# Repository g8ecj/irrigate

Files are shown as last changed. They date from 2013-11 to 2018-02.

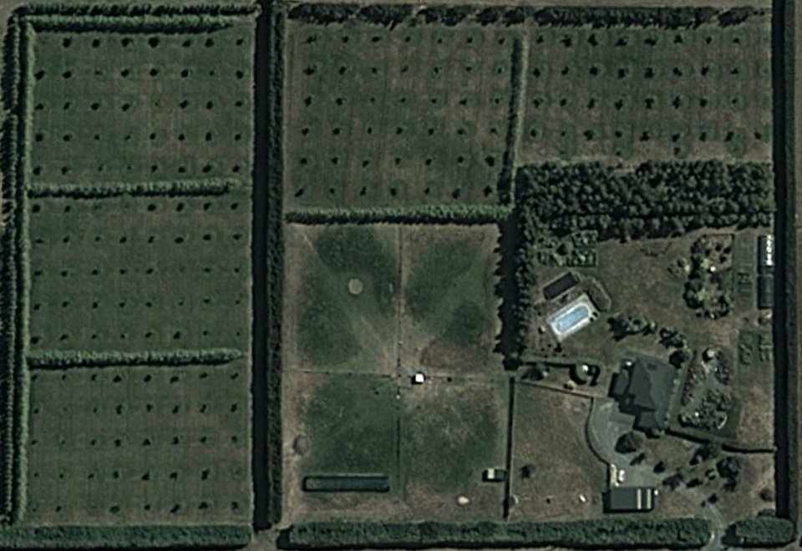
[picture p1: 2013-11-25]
www/zones.jpg

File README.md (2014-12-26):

This is the irrigation controller. It has evolved over a period of some 5 years, the
requirements have changed (and been expanded) and the hardware changed such that a router
no longer requires the warranty invalidated by modifying it with a soldering iron!!

It uses a number of DS2413 1-wire dual channel GPIO chips to drive triacs to operate
valves and pumps. It also optionally monitors 2 temperature sensors to implement 
a preset frost protection program and monitors the current drawn by the valves to 
ensure they are connected correctly.

The 1-wire bus with these devices on it is driven from a DS2480B UART to 1-wire Master 
Controller chip which is connected to one of the serial ports available on a modified
Linksys WRT54GL wireless router. It has also been used with a TPLINK WR1043ND router
and a USB9097 USB 1-wire master dongle.

The router has Open Source software available for it that not only frees the 
user from the limits of the manufacturers code but also provides the cross compile 
environment to allow addition functions to be added by anyone.
See http://openwrt.org

It uses the owfs system that makes 1-wire devices appear as a part of the file system.
The interface to the owlib software is via the owcapi 'C' API library.

These files implement an embedded http server with simple callbacks to the main code. It
is licensed under the GPL V2 License. I'm using version 5.3 at present.
```
   mongoose.c
   mongoose.h
```

These files are totally new and provide all of the AJAX web interface, the onewire interface,
statistics, time event queueing, scheduling, command line parsing and error handling.
They are released under the GNU Public License version 2.
```
   irr_actions.c
   irr_chanmap.c
   irr_onewire.c
   irr_parse.c
   irr_queue.c
   irr_schedule.c
   irr_stats.c
   irr_utils.c
   irr_web.c
   irrigate.c
```
External libraries are used to parse and generate JavaScript Object Notation (JSON) data for the AJAX 
methods used in the web interface. The javascript widgets for timeline support are from 
the CHAPS links library and are available under the Apache license. Other javascript code has
been released to the public domain.

The makefile will do a native build under Linux by defining a 'PC' target that causes a 1-wire simulator
to be built, allowing the web interface to be tested.

Compiling under OpenWrt is simple. Download the latest stable openwrt sources using
```
   'git clone git://git.openwrt.org/14.07/openwrt.git'
```
Unpack the compressed file 'openwrt-package' that provides the package makefile and control files for 
native packaging and copy into the 'package' directory in your openwrt directory maintaining the directory structure.
Install the optional feeds packages to get owfs
```
   './scripts/feeds update -a'
   './scripts/feeds install owfs'
```
and copy the .config file to the top level of openwrt.
```
make oldconfig
make
```

Alternatively, configure the system to build the package by running 'make menuconfig' and select
```
    'Utils' -> 'irrigate'
            -> 'Filesystem' -> 'owfs'
    'Libraries' -> 'libjson'
                -> 'Filesystems' -> 'libow'
                                 -> 'libow-capi'
```
These can all be built as modules or built into the main image.

Kernel modules to consider depend on the 1-wire interface in use. The USB9097 requires the 
'kmod-usb-serial-ch341' module USB/UART driver for example.

Save the new config and then build the whole system using 'make'. Install to the target as a
complete image or using 'opkg' package manager if using modules.

Files to be created/customised are:
```
www/passfile
www/zones.html
www/zones.jpg
www/zones.conf
```

The first is created using the '-A' command line switch, the same as Mongoose in stand-alone mode,
the next 2 describe the layout of the general webpage and the final file describes the 1-wire addesses 
(where appropriate), the characteristics of each zone and where it appears on the browser image map.

```
$ ./irrigate --help
irrigate: Irrigation Controller Version 3.10 Copyright (c) 2009-2014 Robin Gilks
usage: ./irrigate [bcdfhlprstvx]

-a <file>, --file      access log file name
-b,        --background run in daemon mode
-c,        --config    configure zone mapping
-d <dir>,  --datapath  data file directory
-f <file>, --file      config file name
-l <int>,  --limit     degree-minutes before frost program runs
-m,        --monitor   check current drawn by solenoid valves
-p <int>,  --port      http port number
-r <dir>,  --root      http root directory
-s <dev>,  --serialport serial port device
-t <int>,  --threshold temperature below which frost protect operates
-v,        --version   useful version information
-x <int>   --debug     debug mode
-h,        --help      this help screen
```
Example command line:
```
irrigate -m -b -t 0.1 -l 15 -r /www -d /www -f /www/zones.conf -s /dev/tts/1
   * monitor valve current usage
   * run in background as a service
   * threshold temperature for frost protection -0.1C
   * run frost protect after 15 degree-minutes (eg -3C for 5 minutes)
   * root directory /www
   * data directory (hold history, schedule and statistics data)
   * configuration file path and name defined
   * serial port used by modified WRT54GL (second serial port)
```

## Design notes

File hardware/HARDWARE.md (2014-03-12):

The hardware for the irrigation controller consists of a central 'plugboard' which contains the
RJ11 connectors for the standard 1-wire connectors from the 1-wire master and the temperature sensors.

It also contains the ribbon connectors for the zone cards, each of which handles 8 irrigation valves.

The precision rectifier for the current transformer is also on the plugboard, along with the 12v power 
connection for the zone cards.

The zone cards each handle 8 valves and contain 4 off DS2413 dual channel 1-wire switches and 8 triacs
and indicator LEDs.

The PCB layout is optimised for debugging a prototype rather then anything else, the current transformer 
is similarly a prototype, it being a stripped out wall wart stransformer with the seconardy removed
and replaced by 4 turns of wire as a primary to measure the current from the 24volt transformer that
powers the valves.

The power supply for the zone cards and the plugboard is taken from the 12v supply for the router
that provides the CPU!!

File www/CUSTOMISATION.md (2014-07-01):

The UI (User Interface) is 'soft' in that the position of the programming buttons is entirely described
by the web (html) file, the colours of events by the CSS (Cascading Style Sheets) and the positions of
zones on the image map by the configuration file.

The image file can be any jpg or png file, and can be sized to suit the UI required or the UI
could be constructed without an image.

The configuration file is shared by the UI and the server. It contains a list of json objects. These 
consist of a set of lines of the form "key" = "value", some of these keys are used by both UI and 
server, others are exclusive for one or the other.

The configuration file basics can be interactively generated using the -c command line switch. This
will cause the zones to be activated one by one in the order of 1-wire discovery and the user is
prompted for the zone number they wish to allocate to them. This allows the hardware connections
to the various valves and pumps to be defined. The additional data required in the configuration
can then be edited into this skeleton.

Password protect of the UI is handled by a file called passfile in the data directory. An example,
as generated by -A command line switch, for user 'admin', password 'admin' is supplied.

json keys used by UI in html file
```
"zone":             int        index to a specific item
"id":               alphanum   used for diagnostics, etc
"x":                int        % (0-(100-w)) of distance from left of image map
"y":                int        % (0-(100-h)) of distance down from top of image map
"w":                int        % (0-100) width of box drawn no image map
"h":                int        % (0-100) height of box drawn on image map
"selectable":       bool       if the user can select it for programming
"name":             alphanum   plain text displayable name
```

json keys used for normal programable zones
```
"zone":             int        index to a specific item
"id":               alphanum   used for diagnostics, etc
"aorb":             bool       indicates channel A or B on the DS2413 driver
"address":          hexstring  <family>.<serialnumber> 1-wire address
"flow":             int        flow rate in litres/minute
"current":          int        current draw of valve in milliamps
```

json boolean keys that modify a zone
```
"ispump":           bool       zone controls a pump
"isfrost":          bool       frost protection applies
"istest":           bool       is a virtual zone that triggers test mode
"isoutput":         bool       defines a 1-wire device that controls an output
"issensor":         bool       defines a 1-wire device that is read as a sensor
"isspare":          bool       indicates a zone that is not used
```

json keys that pass useful information about a pump
```
"minflow":          int        minimum flow of a pump in litres/minute
"nomflow":          int        nominal flow of a pump in litres/minute
"maxflow":          int        maximum flow of a pump in litres/minute
"maxstarts":        int        maximum number of starts of a pump allowed per hour
"isstock":          bool       pump/feed that supplies taps and stock troughs
"start":            int        time in hhmm format of when to start a pump with the isstock attribute
"end":              int        time in hhmm format of when to stop a pump with the isstock attribute
```

json keys that pass useful information about a sensor
```
"path":             alphanum   string that defines the owfs node to access
"type":             alphanum   what type of sensor: CURRENT, EXTTEMP, INTTEMP, SETTIME, GETTIME
```

json keys that identify virtual zones
```
"group"             int        identifier for a group from 1-15
"zones"             array      list of zones in a group
```

experimental keys
```
"zoom":             int        optional zoom factor. Determines whether to try and show name of the zone
                               doesn't work with image maps very well!!
```

The server responds to requests for '/status' and '/timedata' and the json objects returned
are used in conjunction with CSS style code to set the colour and other attributes.

The 'status' display uses the key "status" for CSS selection and the key "description" for 
the mouseover title that is displayed for each irrigation zone. The following global keys are
also available:
```
"time"              string     time in HH:MM:SS format
"temperature"       int        scaled by 100 to allow local decimal resolution
"current"           int        scaled by 1000 (i.e. mA)
"flow"              int        litre/min
"frost"             string     one of "on", "man", "arm", "run", "off" to indicate current state
```

The 'timeline' display uses the key "status" to determine the type of box displayed in the timeline:
```
"start"             time       defined using the format template "%a, %d %b %Y %H:%M:%S %z"
"end"               time       define the extent of an event
"status"            string     its class is derived from this
"description"       string     is just that! 
"mindate"           time       defines the left limit (i.e. in the past)
"maxdate"           time       define the limits of the display (usually +/- 8 days)
```

Examples

A small zone that runs the misters in a tunnel house
```
"zone":  8                       // arbitrary number from 1 to MAXZONES
"id": "tunnel"                   // label used for debugging
"x": 82                          // how far across from top left
"y": 42                          // how far down
"w":  2                          // quite narrow!!
"h":  6                          // tall
"zoom": 13                       // values > 10 display the whole name in the box
"selectable": true               // can be selected to program
"name": "Tunnel House"           // friendly name
"aorb": true                     // hardware channel PIO.A
"address": "3a.2d3201000000"     // hardware channel owfs format 1-wire address
"flow": 8                        // 8 l/m flow rate
"current": 160                   // draws 160mA
```

A zone that describes the valve that allows the domestic feed to pressurise the irrigation system to run
stock troughs and taps about the place. It also handles low volume irrigation up to the flow rate of the main pump.
```
"zone": 32
"id": "dpfeed"
"x": 62
"y": 65
"w":  2
"h":  2
"zoom": 13
"selectable": false              // not user programable - handled by the server
"name": "Domestic Feed"
"aorb": false
"address": "3a.9b8d03000000"
"ispump": true                   // tell the system its a pump
"isstock": true                  // tell the system it is used by time as well as by demand
"minflow": 1                     // minimum demand level
"nomflow": 100                   // can deliver this amount normally
"maxflow": 100                   // can deliver this much as a maximum
"maxstarts": 720                 // translates to how long to remain off after shutdown
"maxrun": 10800                  // when run by timer, how long in one go to prevent valve sticking
"start": 0700                    // time period for running starts here
"end": 2100                      // - and ends here
"current": 160
"isoutput": true                 // its an output, not a sensor
```

A zone that describes a pump
```
"zone": 16
"id": "well"
"x": 62                          // it appears on the image map 
"y": 68
"w":  2
"h":  3
"zoom": 13
"selectable": false              // but the user can't select it from the UI - operation is automatic
"name": "Well Pump"
"aorb": true                     // 1-wire data of how to control it
"address": "3a.824b01000000"     // not as valve but the contactor that runs it is driven the same way
"ispump": true                   // describes what it is
"minflow": 101                   // flow rate below which the pump switches off
"nomflow": 300                   // when calculating a group, how much should be done at once
"maxflow": 9999                  // stop it complaining if manually more is scheduled than nominal flow
"maxstarts": 20                  // locks for 3 mins when stopped to prevent abuse
"maxrun": 43200
"current": 120
"isoutput": true
```

A (virtual) zone that has no direct valves but instead holds a group of zones. It appears on the UI and can be programmed
(hence selectable) 
```
"zone": 40
"id": "allnuts"
"x": 87"y": 5
"w": 12
"h": 10
"zoom": 3
"selectable": true
"name": "All Walnuts"
"group": 1                       // a numeric 'handle' for the group (a zone can be in more than 1 group)
"zones": [1, 2, 3, 4, 5]         // list of zones in the group
```

Another virtual zone that has no valves but in this case operates on a specific internal function (test mode)
```
"zone": 43
"id": "test"
"x": 87
"y": 92
"w": 12
"h":  5
"zoom": 3
"selectable": true
"name": "Test Valves"
"istest": true                   // say what it does
```

A temperature sensor implemented with a DS18B20
```
"zone": 51
"id": "sensor2"
"x":  0                          // none of the positioning data is used
"y":  0
"w":  0
"h":  0
"zoom": 3
"selectable": false
"name": "Sky Temperature"
"address": "28.620A62050000"    // how to find the device on the 1-wire bus
"path": "/%s/temperature"       // how to addess the capability
"issensor": true                // say what it is
"type": "exttemp"               // say what type it is
```

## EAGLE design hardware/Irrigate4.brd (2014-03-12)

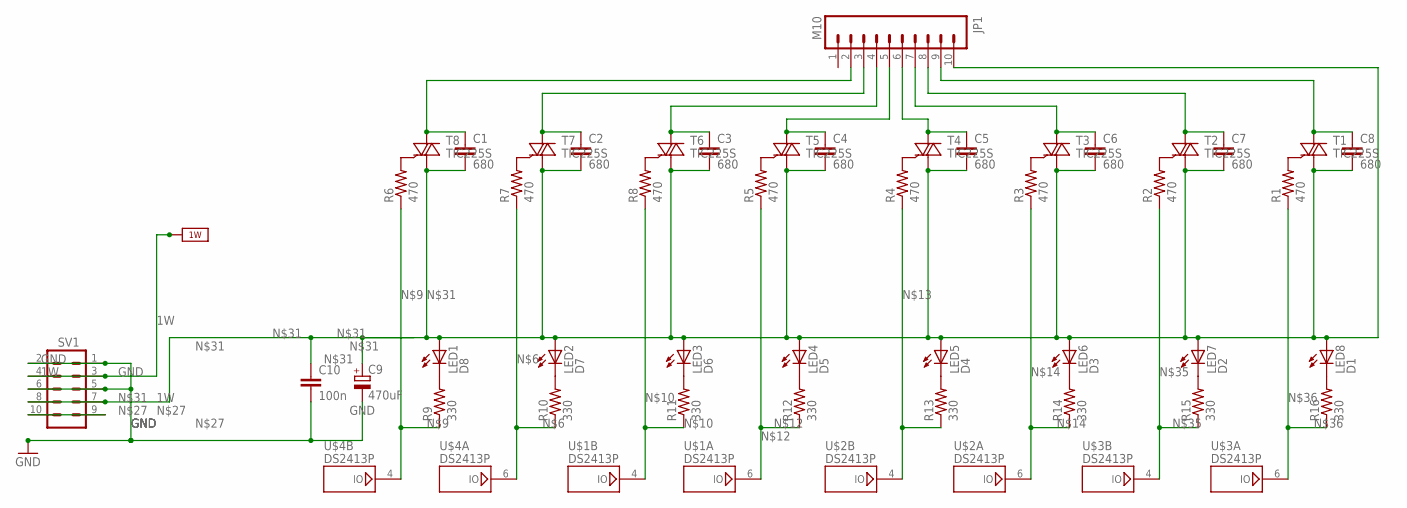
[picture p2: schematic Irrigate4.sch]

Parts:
C1, C2, C3, C4, C5, C6, C7, C8: 680; C050-045X075
C9: 470uF; E5-8,5
C10: 100n; C050-024X044
JP1: M10; 10X10MM
LED1: D8; LED3MM
LED2: D7; LED3MM
LED3: D6; LED3MM
LED4: D5; LED3MM
LED5: D4; LED3MM
LED6: D3; LED3MM
LED7: D2; LED3MM
LED8: D1; LED3MM
R1, R2, R3, R4, R5, R6, R7, R8: 470; AXIAL-0.3
R9, R10, R11, R12, R13, R14, R15, R16: 330; AXIAL-0.3
SV1: M05X2PTH; AVR_ICSP
T1, T2, T3, T4, T5, T6, T7, T8: TIC225S; TO220DS
U$1, U$2, U$3, U$4: DS2413P; TSOC6

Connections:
1W: SV1.3, SV1.4, U$1.2 (1W), U$2.2 (1W), U$3.2 (1W), U$4.2 (1W)
GND: C9.-, C10.2, SV1.1, SV1.2, SV1.5, SV1.6, U$1.1 (GND), U$1.5 (GND), U$2.1 (GND), U$2.5 (GND), U$3.1 (GND), U$3.5 (GND), U$4.1 (GND), U$4.5 (GND)
unnamed: R1.P$2 (2), T1.G
unnamed: R2.P$2 (2), T2.G
unnamed: R3.P$2 (2), T3.G
unnamed: R4.P$2 (2), T4.G
unnamed: R5.P$2 (2), T5.G
unnamed: R7.P$1 (1), R10.P$1 (1), U$4.6 (IO)
unnamed: R7.P$2 (2), T7.G
unnamed: R6.P$2 (2), T8.G
unnamed: R6.P$1 (1), R9.P$1 (1), U$4.4 (IO)
unnamed: R8.P$1 (1), R11.P$1 (1), U$1.4 (IO)
unnamed: R8.P$2 (2), T6.G
unnamed: R5.P$1 (1), R12.P$1 (1), U$1.6 (IO)
unnamed: R4.P$1 (1), R13.P$1 (1), U$2.4 (IO)
unnamed: R3.P$1 (1), R14.P$1 (1), U$2.6 (IO)
unnamed: LED5.K (C), R13.P$2 (2)
unnamed: LED6.K (C), R14.P$2 (2)
unnamed: LED7.K (C), R15.P$2 (2)
unnamed: C8.1, JP1.9, T1.A2
unnamed: C7.1, JP1.8, T2.A2
unnamed: C6.1, JP1.7, T3.A2
unnamed: C5.1, JP1.6, T4.A2
unnamed: C4.1, JP1.5, T5.A2
unnamed: C3.1, JP1.4, T6.A2
unnamed: C2.1, JP1.3, T7.A2
unnamed: C1.1, JP1.2, T8.A2
unnamed: LED8.K (C), R16.P$2 (2)
unnamed: SV1.9, SV1.10
unnamed: LED1.K (C), R9.P$2 (2)
unnamed: LED2.K (C), R10.P$2 (2)
unnamed: C1.2, C2.2, C3.2, C4.2, C5.2, C6.2, C7.2, C8.2, C9.+, C10.1, JP1.10, LED1.A, LED2.A, LED3.A, LED4.A, LED5.A, LED6.A, LED7.A, LED8.A, SV1.7, SV1.8, T1.A1, T2.A1, T3.A1, T4.A1, T5.A1, T6.A1, T7.A1, T8.A1
unnamed: LED3.K (C), R11.P$2 (2)
unnamed: LED4.K (C), R12.P$2 (2)
unnamed: R2.P$1 (1), R15.P$1 (1), U$3.4 (IO)
unnamed: R1.P$1 (1), R16.P$1 (1), U$3.6 (IO)

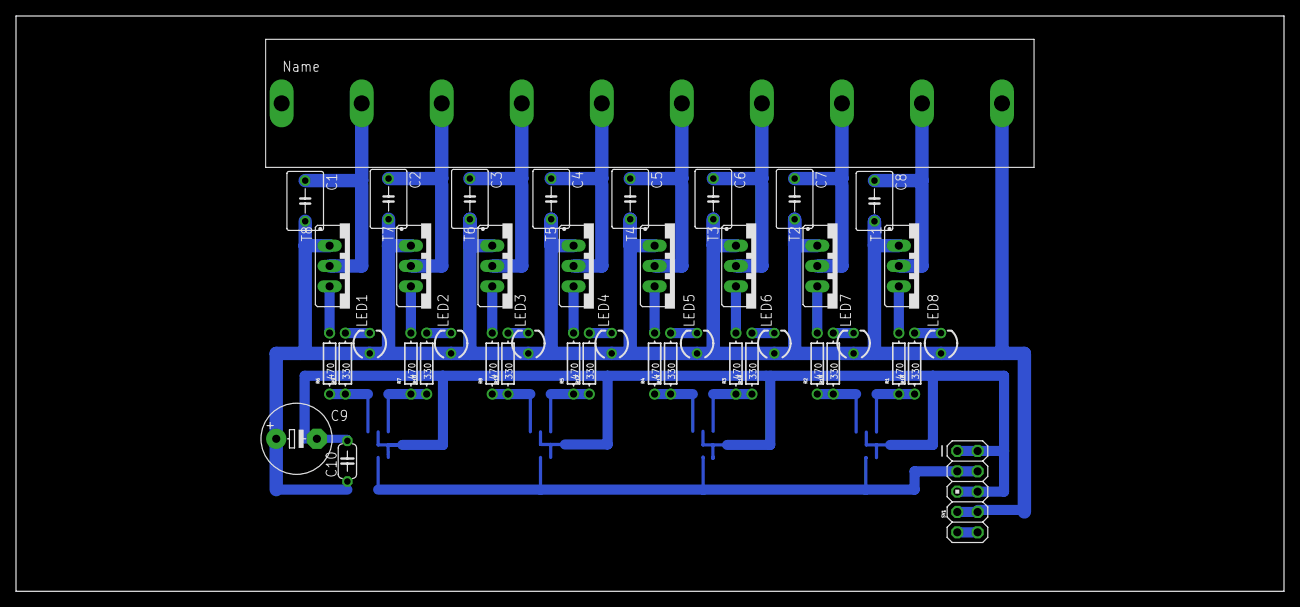
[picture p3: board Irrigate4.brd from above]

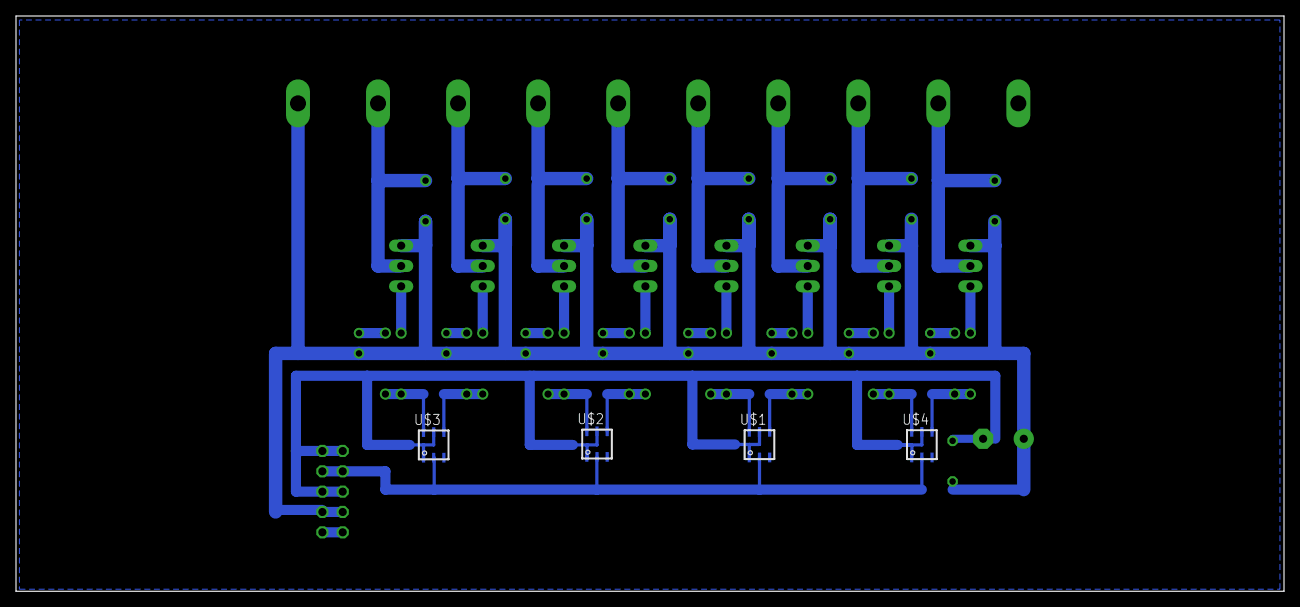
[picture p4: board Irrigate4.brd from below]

Board: 2 copper layers, 158.4 x 71.9 mm, 48 parts (4 on the bottom side), 36 nets.

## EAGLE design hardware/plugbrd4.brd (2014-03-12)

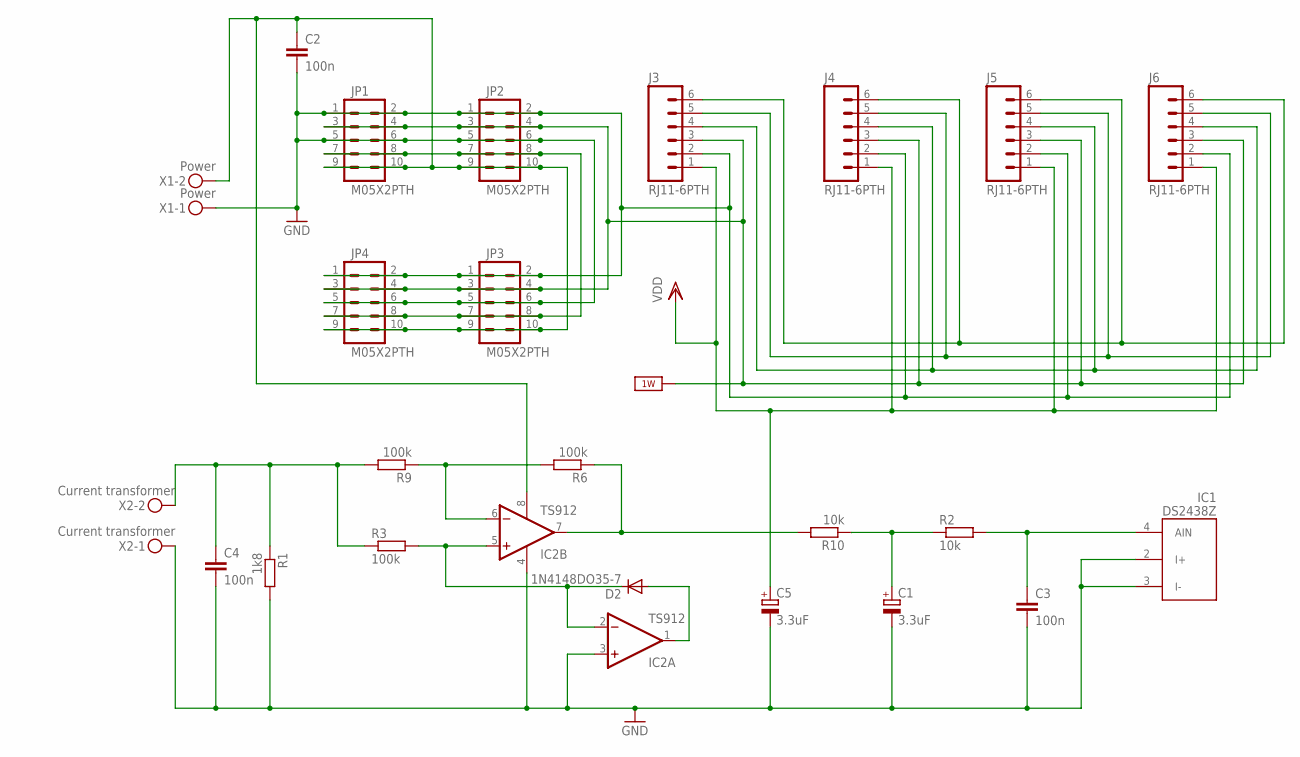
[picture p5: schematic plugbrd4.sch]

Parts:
C1, C5: 3.3uF; E5-6
C2, C3, C4: 100n; C050-025X075
D2: 1N4148DO35-7; DO35-7
IC1: DS2438Z; SO08
IC2: TS912; SO08
J3, J4, J5, J6: RJ11-6PTH; RJ11-6
JP1, JP2, JP3, JP4: M05X2PTH; AVR_ICSP
R1: 1k8; 0207/12
R2, R10: 10k; 0207/12
R3, R6, R9: 100k; 0207/12
X1: Power; MKDSN1,5/2-5,08
X2: Current transformer; MKDSN1,5/2-5,08

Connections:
1W: IC1.8 (1W), J3.3, J4.3, J5.3, J6.3, JP1.3, JP1.4, JP2.3, JP2.4, JP3.3, JP3.4, JP4.3, JP4.4
GND: C1.-, C2.2, C3.2, C4.2, C5.-, IC1.1 (GND), IC1.2 (I+), IC1.3 (I-), IC2.3 (+IN), IC2.4 (V-), J3.2, J4.2, J5.2, J6.2, JP1.1, JP1.2, JP1.5, JP1.6, JP2.1, JP2.2, JP2.5, JP2.6, JP3.1, JP3.2, JP3.5, JP3.6, JP4.1, JP4.2, JP4.5, JP4.6, R1.2, X1.1, X2.1
unnamed: C1.+, R2.1, R10.1
unnamed: JP1.7, JP1.8, JP2.7, JP2.8, JP3.7, JP3.8, JP4.7, JP4.8
unnamed: D2.A, IC2.1 (OUT)
unnamed: J3.4, J4.4, J5.4, J6.4
unnamed: J3.5, J4.5, J5.5, J6.5
unnamed: J3.6, J4.6, J5.6, J6.6
unnamed: IC2.7 (OUT), R6.1, R10.2
unnamed: IC2.6 (-IN), R6.2, R9.1
unnamed: C4.1, R1.1, R3.1, R9.2, X2.2
unnamed: C2.1, IC2.8 (V+), JP1.9, JP1.10, JP2.9, JP2.10, JP3.9, JP3.10, JP4.9, JP4.10, X1.2
unnamed: C3.1, IC1.4 (AIN), R2.2
unnamed: D2.C, IC2.2 (-IN), IC2.5 (+IN), R3.2
VDD: C5.+, IC1.5 (VDD), J3.1, J4.1, J5.1, J6.1

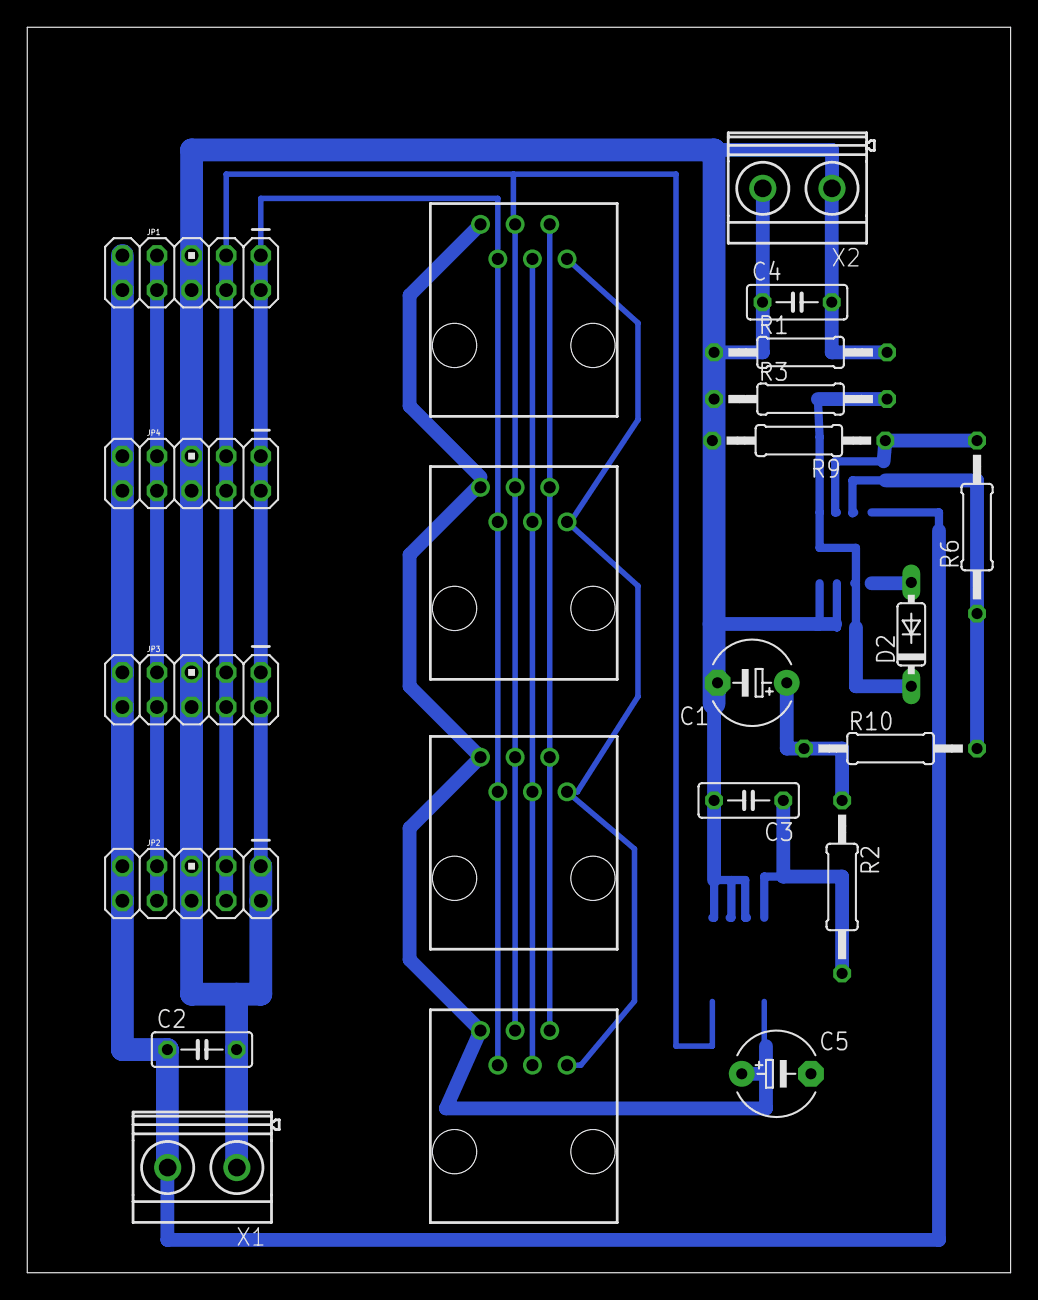
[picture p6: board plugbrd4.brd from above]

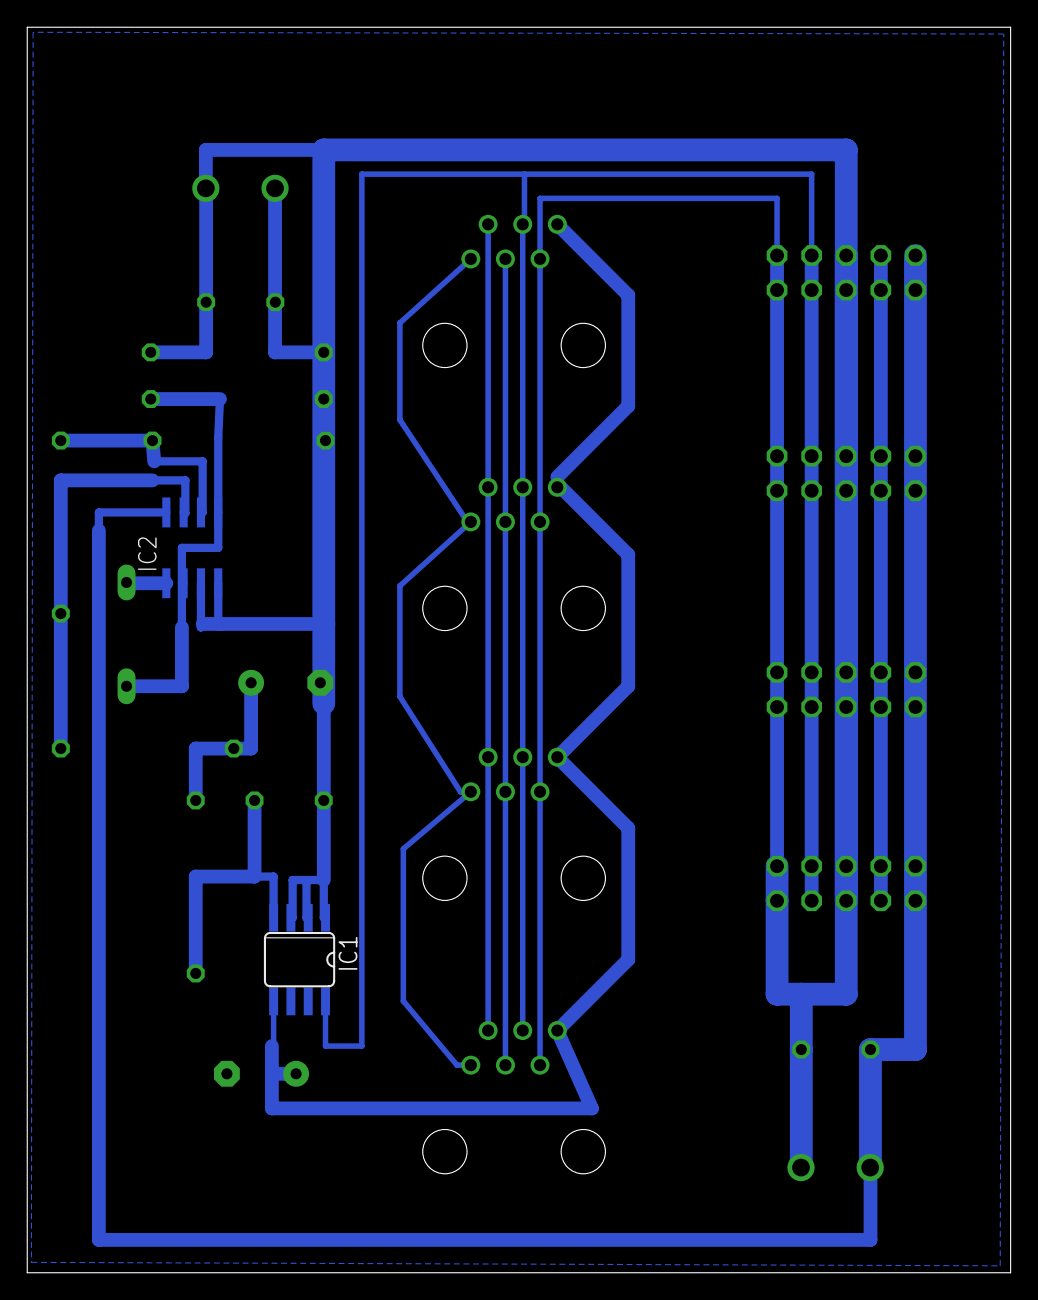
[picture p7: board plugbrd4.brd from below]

Board: 2 copper layers, 72.2 x 91.4 mm, 24 parts (2 on the bottom side), 15 nets.

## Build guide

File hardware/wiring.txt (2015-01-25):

Various 3 core cables have been used to make up multicore round the garden and orchards.
The cables are colour coded and the common wire may be in a different cable to the active wire.
In both cases the wire and the common are identified by both cable and conductor colours.

    zone       name          cable colour     wire colour        Common  (cable/conductor)

     1       "Walnuts 1"        Red              Red             Red/Black

     2       "Walnuts 2"        Red              Green           Red/Black

     3       "Walnuts 3"        Black            Green           Black/Black

     4       "Walnuts 4"        NA               Green           NA/Black

     5       "Walnuts 5"        NA               Red             NA/Black

     6       "Willows"          Black            Red             Black/Black

     7       "Veg Plot 1"       Red              Black           Red/Red

     8       "Tunnel House"     Red              Green           Red/Red

     9       "Shade House"      Yellow           Red             Black/Black

    10       "Veg Plot 2"       Black            Green           Black/Black

    11       "Veg Plot 3"       Black            Red             Black/Black

    12       "Long Border"      Green            Red             Red/Red

    13       "Native Border"    Blue             Black           Red/Red

    14       "Firewood"         Blue             Green           Red/Red

    15       "Chook Border"     Green            Black           Red/Red

    16       "Well Pump"        xxxx

    17       "Cottage Garden"   Blue             Red             Red/Red

    18       "Quake Garden"     Yellow           Black           Black/Black

    19       "Big Gun"          small            Red             small/Bl+Wh

    20       "spare01"          small            Green           small/Bl+Wh

    21       "Wasabi"           small            Yellow          small/Bl+Wh

    22       "Pool topup"       cat5

    32       "Domestic Feed"    xxxx

Yellow/Green is spare - routed to Quake garden
Green/Green is spare

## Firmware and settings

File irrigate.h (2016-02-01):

//---------------------------------------------------------------------------
// Copyright (C) 2009-2014 Robin Gilks
//
//
//  irrigate.h   -   Function prototypes, global variables and #defines!!
//
//             0.70 - split into several files
//
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



#include <stdint.h>
#include <stdbool.h>
#include <stdio.h>
#include <stdlib.h>
#include <unistd.h>
#include <errno.h>
#include <sys/types.h>
#include <sys/stat.h>
#include <time.h>
#include <string.h>
#include <syslog.h>
#include <json-c/json.h>

#include "mongoose.h"

#define VERSION "4.50"

#define UNUSED(arg) (arg) __attribute__ ((unused))


// Constant definitions
#define DS18S20_FAMILY_CODE       0x10
#define DS18B20_FAMILY_CODE       0x28
#define DS1822_FAMILY_CODE        0x22

#define DS2413_FAMILY_CODE        0x3A
#define DS2438_FAMILY_CODE        0x26
// number of 1-wire devices of any one type
#define MAXDEVICES         20
// arbitrary number of pumps
#define MAXPUMPS 10
// number of sensors
#define MAXSENSORS 20

#define MAXDEVLEN 80
#define MAXFILELEN 80

#define VIRTUALZONES 10
//#define REALZONES (MAXDEVICES * 2)
#define REALZONES 100
#define MAXZONES (REALZONES + VIRTUALZONES)
#define MAXGROUPS 16
/* enumerate virtual zones */
#define FROST_LOAD   (REALZONES + 1)
#define RESCHEDULE   (REALZONES + 2)
#define RESET        (REALZONES + 3)


#define FROST_TIME 60
#define VALVE_OVERLAP 1
#define VoltToMilliAmp 275

// times used in action stuff
#define FAILED_RETRY 60

extern const char *fmt;

extern char sensornames[][9];

typedef enum
{
   eCURRENT = 1,
   eEXTTEMP,
   eINTTEMP,
   eSETTIME,
   eGETTIME,
   eMAXSENSE
} eSENSOR;



/*
 Must put some info in here!!
*/



struct mapstruct
{
   uint8_t zone;                // replicates the index into the map array
   uint16_t valid;              // bit ORed for validation of the zone in various modes
   uint8_t useful;              // whether the zone has useful scheduling data in it
   uint8_t output;              // track the actual state of the output. One of OFF, ON, TEST
                                // + used for user input while configuring the hardware
   uint8_t dev;                 // device index into the address array
   uint8_t AorB;                // whether this zone is on port A (TRUE) or B of the IO chip
   char address[17];            // 8 byte chip address in hex - derived from famsw[dev]? includes null terminator
   char name[33];               // up to 32 chars free format name string
   uint8_t state;               // if currently on or off - used when toggling an object
   time_t duration;             // total of how long a zone is active for
   time_t period;               // the working value of how long to be on for on this pass
   time_t lastrun;              // the last time the zone was activated
   time_t lastdur;              // the last time the zone was activated
   int32_t frequency;           // how often the zone is activated
   uint8_t locked;              // > 0 if locked (only really applies to a pump)
   uint16_t flow;               // nominal flow rate
   time_t starttime;            // when this zone will start
   time_t actualstart;          // when this zone actually started (may have been delayed by a power reset)
   double totalflow;            // total flow seen on this zone during this run
   uint16_t type;               // bit ORed for pump, frost bits
   uint16_t group;              // what groups the zone is in
   uint16_t current;            // expected current draw in mA
   uint8_t link;                // used to map to pump or sensor list
   int lasterrno;               // copy of last system errno
   uint8_t daylist[8];          // what days to operate
};


struct pumpstruct
{
   uint8_t zone;               // links back to chanmap
   uint16_t minflow;           // minimum flow
   uint16_t nomflow;           // nominal flow
   uint16_t maxflow;           // maximum flow
   uint16_t maxstarts;         // how often pump can be started
   uint32_t maxrun;            // how long the pump can run for in one go
   uint16_t start;             // start time when pump is allowed to run (in HHMM format)
   uint16_t end;               // end time for running pump (HHMM)
   uint32_t pumpingtime;       // how long we spent running the pump in this session
};


struct sensorstruct
{
   uint8_t zone;
   uint8_t type;
   char path[33];
};


// what 'state' we are in
#define IDLE      0
#define ACTIVE    1
#define ERROR     2
// List of actions saved in the history file used to provide the retrospective timeline display
// follow on from state values!!
#define WASOK      3
#define WASCANCEL  4
#define WASFAIL    5

// what an output can do
#define OFF       0
#define ON        1
#define TEST      2


// what 'type' attributes a zone has
#define ISPUMP   1
#define ISFROST  2
#define ISGROUP  4              // first bit of several groups possible
#define ISSTOCK  8
#define ISTEST   16
#define ISSENSOR 32
#define ISOUTPUT 64
#define ISSPARE  256

// what state the frost protect can be in
#define FROST_OFF    1
#define FROST_MANUAL 2
#define FROST_ACTIVE 3

// what validation bits are used
#define HARDWARE 1              // the hardware actually exists for this zone
#define CONFIGURED 2            // exists in the config file so operate on it



// ordered time queue
typedef struct tqueue
{
   time_t starttime;            // when this object is acted on
   uint8_t zone;                // the object number
   uint8_t action;              // what action is to happen on expiry
   struct tqueue *next;         // the next object in the list
} TQ;

//actions
#define NOACTION 0
#define TURNON   1
#define TURNOFF  2
#define CANCEL   3
#define TESTON   4
#define TESTOFF  5
#define UNLOCK   6
#define PUMPOFF  7


// globals that all in this module can see
extern time_t basictime;
extern time_t ampstime;
extern struct mapstruct chanmap[];
extern struct pumpstruct pumpmap[];
extern struct sensorstruct sensormap[];
extern int8_t wellzone;
extern int16_t wellmaxflow;
extern int16_t wellmaxstarts;
extern uint8_t frost_mode;
extern bool frost_armed;
extern bool monitor;
extern int16_t interrupt;
extern double temperature;
extern double Tintegral;
extern char daystr[][10];
extern time_t startuptime;

// config items
extern int16_t debug;
extern bool timestamp;
extern bool fileflag;
extern bool background;
extern bool config;
extern char device[];
extern char configfile[];
extern char datapath[];
extern char httpport[];
extern char httproot[];
extern char accesslog[];
extern double Tthreshold;
extern uint16_t frostlimit;

// prototypes

// queuing functions
void insert (time_t starttime, uint8_t zone, uint8_t action);
bool delete (uint8_t zone);
time_t findonqueue (uint8_t zone);
uint8_t peek_queue(uint8_t *action);
uint8_t walk_queue(uint8_t index, uint8_t * zone, time_t * starttime, uint8_t *action);



// action routines

void doaction (uint8_t zone, uint8_t action);
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

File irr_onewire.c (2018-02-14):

//---------------------------------------------------------------------------
// Copyright (C) 2009-2014 Robin Gilks
//
//
//  irr_onewire.c   -   This section looks after the 1-wire interface
//
//             0.70 - split into several files
//
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

#include <owcapi.h>

#include "irrigate.h"


char devcopy[MAXDEVICES][16];
uint8_t numgpio = 0;
uint8_t numvolt = 0;
uint8_t numtemp = 0;

// define the following if using a version of OWFS prior to 2.9p3
// which has a problem with big endian handling of aggregate PIO devices (e.g. DS2408, DS2413)
#define OW_ENDIAN_BUG 1

#ifdef PC
uint16_t testcurrent = 0;


/* these are a set of dummy functions that are used when compiled for a PC
 * that has no 1-wire devices attached */
uint16_t
irr_onewire_init (void)
{
   return TRUE;
}

void
irr_onewire_stop (void)
{
}

bool
//DoOutput (uint8_t UNUSED (zone), uint8_t UNUSED (state))
DoOutput (uint8_t zone, uint8_t state)
{
   chanmap[zone].output = state;     // the real code doesn't do this - we have to save state so we can fake the current
   return TRUE;
}

void general_reset(void)
{
}

void
irr_onewire_match (uint16_t UNUSED (numgpio))
{
   int i;
   for (i = 1; i < REALZONES; i++)
      if (chanmap[i].valid & CONFIGURED)
         chanmap[i].valid |= HARDWARE;  // got real hardware here
}

uint16_t
GetCurrent (void)
{
   int zone;
   uint16_t mycurrent = 0;

   for (zone = 1; zone < REALZONES; zone++)
   {
      if (debug > 0)
      {
         if (((chanmap[zone].output == ON) || (chanmap[zone].output == TEST)) && (zone != 3))      // fail zone 3 for testing
            mycurrent += chanmap[zone].current;
      }
      else
      {
         if ((chanmap[zone].output == ON) || (chanmap[zone].output == TEST))
            mycurrent += chanmap[zone].current;
      }
   }
   if (testcurrent)
   {
      testcurrent--;
      return 88;
   }
   else
      return mycurrent;
}

double
GetTemp(void)
{
   return 0;
}

double
GetSensorbyZone(uint8_t zone)
{
   return zone * 4;
}

void
setGPIOraw(uint8_t UNUSED (index), uint8_t UNUSED (value))
{
}

char *
getGPIOAddr (uint8_t UNUSED (index))
{
   return "1122334455667788";
}

#else

/*
 * The real code follows now!!
 */


// this function relies on chanmap_read having already been called to load up the 
// chanmap with details of what devices should be present
uint16_t
irr_onewire_init (void)
{
   uint8_t numdev = 0;
   int16_t family;
   char * tokenstring;
   size_t s ;
   char seps[] = ",";
   char* token;
   char val[10];

   if (OW_init(device))
   {
      log_printf (LOG_EMERG, "Error: failed to acquire port");
      exit (EXIT_FAILURE);
   }

   OW_set_error_print("2");
   sprintf(val, "%d", debug);
   OW_set_error_level(val);
// get a list of the top of the 1-wire tree to see what devices there are
   OW_get("/",&tokenstring,&s) ;

   token = strtok (tokenstring, seps);
   while (token != NULL)
   {
// keep a copy of the addresses of the devices we find and catagorise them
      if (token[2] == '.')
      {
         token[15] = '\0';
         if (debug)
            log_printf (LOG_INFO, "Device %s", token);
         strncpy(devcopy[numdev++], token, 16);
         family = strtol(token, NULL, 16);
         switch (family)
         {
         case DS2413_FAMILY_CODE:
            numgpio++;
            break;
         case DS2438_FAMILY_CODE:
            numvolt++;
            break;
         case DS18S20_FAMILY_CODE:
         case DS18B20_FAMILY_CODE:
         case DS1822_FAMILY_CODE:
            numtemp++;
            break;
         }
      }
      token = strtok (NULL, seps);
   }
   free(tokenstring);

   if (numdev == 0)
   {
      log_printf (LOG_EMERG, "Error: nothing found on 1-wire bus - check cables?");
      exit (EXIT_FAILURE);
   }

   log_printf (LOG_INFO, "Found %d GPIO chip(s) OK", numgpio);
   log_printf (LOG_INFO, "Found %d voltage monitor chip(s) OK", numvolt);
   log_printf (LOG_INFO, "Found %d temperature monitor chip(s) OK", numtemp);

   // clear all hardware outputs down
   general_reset ();


   return numdev;
}

void irr_onewire_match (uint16_t numdev)
{
   uint8_t dev, zone;
   // match the values I've read from the file with the devices I scanned and match them up
   for (zone = 1; zone < REALZONES; zone++)
   {
      for (dev = 0; dev < numdev; dev++)
      {
         if (strncasecmp (chanmap[zone].address, devcopy[dev], 15) == 0)
         {
            if (debug)
            {
               if (chanmap[zone].type & ISSENSOR)
               {
                  printf ("Match at zone %d (%s) device %d address %s sensor type %s\n", 
                       zone, chanmap[zone].name, dev, chanmap[zone].address, sensornames[sensormap[chanmap[zone].link].type]);
               }
               else
               {
                  printf ("Match at zone %d (%s) device %d port %c 1-wire address %s\n", 
                       zone, chanmap[zone].name, dev, chanmap[zone].AorB ? 'A' : 'B', chanmap[zone].address);
               }
            }
            chanmap[zone].valid |= HARDWARE;       // got real hardware here
            chanmap[zone].dev = dev;
         }
      }
   }
}

#if OW_ENDIAN_BUG
ssize_t OW_pio_workaround(uint8_t zone, uint8_t state)
{
   static uint8_t iocache[MAXDEVICES] = {0,0,0,0,0,0,0,0,0,0,0,0,0,0,0,0,0,0,0};
   char path[32];
   char val[10];
   uint8_t ioval, index = chanmap[zone].dev;
   ssize_t ret;

   sprintf(path, "/%s/PIO.BYTE", chanmap[zone].address);

   if (chanmap[zone].AorB)
   {
      // operating on PIOA - need current state of B with A bit cleared to activate it
      if (state == OFF)
         ioval = iocache[index] & 0xfe;
      else
         ioval = iocache[index] | 0x01;
   }
   else
   {
      // operating on PIOB
      if (state == OFF)
         ioval = iocache[index] & 0xfd;
      else
         ioval = iocache[index] | 0x02;
   }

   sprintf(val, "%d", ioval);

   ret = OW_put(path, val, strlen(val));
   // if the write worked then update the cache
   if (ret >=0)
      iocache[index] = ioval;

   return ret;
}
#endif


void general_reset(void)
{
   int16_t i;
   char path[32];
   char val[10] = "0,0";

   for (i = 1; i < REALZONES; i++)
   {
      if (chanmap[i].type & ISOUTPUT)
      {
         sprintf(path, "/%s/PIO.ALL", chanmap[i].address);
         OW_put(path, val, strlen(val)) ;
      }
   }
}




void
irr_onewire_stop (void)
{
   OW_finish() ;
}

// read the value of a sensor indexed by the zone
double
GetSensorbyZone(uint8_t zone)
{
   uint8_t sensor;
   double value = 0;
   ssize_t ret;
   char path[32];
   char * tokenstring;
   size_t s;

   sensor = chanmap[zone].link;
   sprintf(path, sensormap[sensor].path, chanmap[zone].address);
   ret = OW_get(path,&tokenstring,&s);
   if (ret >= 0)
   {
      value = atof(tokenstring);
      free(tokenstring);
   }
   return value;
}
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

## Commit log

2013-12-25 Move calculation of total flow from being on-the-fly to polling all active zones Extract expected current poll to a function in the utils section
2013-12-25 Update current values for 22volt supply rather than old 25.5 volt (was blowing vavle solenoids)
2013-12-25 Correctly change current values - got it wrong!!
2013-12-25 Update well pump current draw and include totalflow in status data to web client
2013-12-27 Add an extra element to display the total flow on the main page
2014-01-07 Fix up problems with debug (PC) mode and test changes
    [irr_onewire.c]
2014-01-09 Remove web mutex, correct options so web server starts
    [irrigate.h]
2014-01-13 Fix up locking of domestic feed when in valve test mode
2014-01-14 Improve locking of the well pump and domestic feed during test mode
2014-01-16 Try and get well pump status during test mode to display correctly
2014-01-16 Remove command line driven test mode - interactive one is more powerful now
2014-02-17 Remove redundant file, update sample timedata to latest format
2014-02-18 Total rehash for owfs 1-wire interface
2014-02-18 Remove remaining public domain 1-wire interface headers etc
2014-02-19 Clean compile stage, not debugged yet...
2014-02-19 Keep device addresses in ASCII, example data in config
2014-02-19 Make the best use of the owfs PIO handling. Fail if 1-wire port not available
    [irr_onewire.c]
2014-02-20 New format 1-wire addresses, reduce debug level
2014-02-20 Get sense of bits in general reset the right way up
    [irr_onewire.c]
2014-02-20 Exit if nothing found on 1-wire bus
2014-02-21 Allow for TEST state when turning on a valve
2014-02-23 Minor debug changes, case insensitive compare on 1-wire addresses, extend RX timeout on serial interface
2014-02-23 Unlock well pump if test mode cancelled, turn on valves in test mode
2014-02-23 Clean up locked mouseover and use proper unlock of well pump when test mode cancelled
2014-02-23 Correct version number and display locked status correctly
    [irrigate.h]
2014-02-23 Various temp fixes to investigate 1-wire problems!
    [irr_onewire.c]
2014-02-23 Various bodges to try and fix owfs problems.
    [irr_onewire.c]
2014-02-24 No need to set cache timeout to zero if using uncached tree, memory leak in get_temperature
    [irr_onewire.c]
2014-02-27 Stray locked status from history items and correct OW_put call
    [irr_onewire.c]
2014-03-01 Highlight errors in timeline display using box, tidy main include
    [irrigate.h]
2014-03-02 May be a while before owfs endian bug gets fixed so make a fix here wrapped in a #define
    [irr_onewire.c]
2014-03-03 Start to define how to customise the display, build 1-wire sim by default on PC
2014-03-03 Update CUSTOMISATION.md
    Example pump
2014-03-03 Describe -c switch to create basic config file
2014-03-11 Missing bracket!!
2014-03-11 First cut at merging in new version 5.3 of mongoose
2014-03-12 The hardware files, being Eagle PCB schematics and layouts.
    [Irrigate4.brd, Irrigate4.sch, plugbrd4.brd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]
2014-03-19 Work in progress for new pump handling
2014-03-19 Pump management still not quite right but mostly there now!!
2014-03-20 Looks like the pump algorithm is OK now. Uses new 'stock' flag to indicate a pump is used to supply stock water as well as irrigation
2014-03-20 Handle groups using nominal flow from a pump, just use maximum for scheduling
2014-03-20 Document the changes to pump handling that make it generic
2014-03-22 Version number update to track new pump handling
2014-03-23 Read/write of time to ds2438 doesn't require uncached access
    [irr_onewire.c]
2014-03-24 Start to integrate DS18x20 temperature sensors into the scheme of things
2014-03-24 Allocate ds18x20 temperature sensors in preference to the ones in the ds2438 chips
2014-03-24 Fix syntax error in target (non-PC) build
    [irr_onewire.c]
2014-03-24 Make 1-wire family codes consistent
2014-03-27 Changes to pump handling to define a maximum run time for a pump
2014-03-27 Allow for more than 1 pump in the statistics recording
2014-03-27 Pump time getting mixed up between seconds and hours of run time in the stats file
2014-03-31 Optimise pump stats
2014-04-02 Correct was_is decision in status description and reload status when switching from timeline screen
2014-04-03 Use a bit pattern to choose between temperature sensors
2014-04-03 Update temperature sensor index correctly
    [irr_onewire.c]
2014-04-04 Change default maxrun for stock water pump
2014-04-07 Major rework on 'useful' flag to get schedule exiry working again, minor rename of functions
    [irrigate.h]
2014-04-08 Start to make sensors configurable, make sure 'useful' flag changes don't affect display
2014-04-11 Start of config for sensors, read them in, diagnostic printout
2014-04-13 More updates for configurable sensors
2014-04-15 Major changes to differentiate between 1-wire devices from the configuration file rather than just looking at what type they are (which says nothing of what they are doing!) This has simplified lots 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
2014-04-15 Correct 1-wire simulator for PC test mode
    [irr_onewire.c]
2014-04-15 Get some real 1-wire addresses for sensors into the default config
2014-04-15 Convert set/get time to use new sensor style config
2014-04-16 Change sensor type to a string and then parse the string.
2014-04-21 make a cross reference from zone chanmap to the pump and sensor maps
2014-05-01 Adjust title of Program button - needs more work!!
2014-05-02 Finish tidy up of program timeline screen switching
2014-05-24 If pump turn-on fails then wait locktime before retry. Update docs on new pump json keys
2014-06-16 Try and put a duration value into timeline active pump data
2014-06-17 Fine tune the timedata on active pumps
2014-06-17 More bugs in embedded compile
    [irr_onewire.c, irrigate.h]
2014-07-02 Optimise uptime code, don't report sensors in status data
2014-07-04 Tidy up error handling and report failure cause in history display
    [irr_onewire.c, irrigate.h]
2014-07-09 Improve time display of active pump mouseover
2014-08-11 Extend failure lock time to 1 minute
    [irrigate.h]
2014-08-14 Update version, track zone for repeating history items
2014-08-20 All the basics for getting JSON data from the sensors to the AJAX browser frontend
2014-09-28 Split out sensor reading into its own callback, up version
2014-09-28 Remove RTC from sensor status, fix bugs!
2014-09-29 Create more specific json objects for sensors
2014-10-17 Use actualtime not starttime for calculating flow
2014-11-20 Implement 'last time run' for all zones in case I forget what went when!
2014-11-30 Protect password file, improve title display of currentlyactive zone(s)
2014-12-25 Split stats update to allow web interface to construct a human readable set of stat values as well as maintaining the statistics file. Make sure all relevant information is stored in the statistics f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
    [irrigate.h]
2014-12-25 Display factions of an hour correctly, up version number
    [irrigate.h]
2014-12-26 Put wiring info in the correct place
2015-01-22 Use the same methods for statistics display for the log display. Simplify display choice button.
2015-01-25 Put some comments into wiring file.

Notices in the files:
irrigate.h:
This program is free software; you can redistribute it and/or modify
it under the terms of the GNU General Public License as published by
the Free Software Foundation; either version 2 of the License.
